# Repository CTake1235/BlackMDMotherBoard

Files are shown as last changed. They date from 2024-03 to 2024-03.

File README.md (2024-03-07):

# 黒MDマザーボード設計構想
> by しーたけ @C_Take_e
> since 2024/03/05
## 黒MDとは？
```
茨城高専ロボット部にて2017年に開発・製造されたMD。レジストが黒いのでそう呼ばれている。
定格12V駆動。I2C信号またはRS-485で動作する（基本I2Cでしか使わん）。
ロボコンで用いる各種モータを振り回せるため、何も考えずに使いまわされ続けている。
```
## コンセプト
- **やさしいマザボ**
## 詳細な構想
- ケーブルを介した連結が可能な、4枚挿しコンパクトマザボ
	- 単純なケーブルでできる、「マザー連結用」のようなケーブルを不要とする
	
- 黒MD初期マザーに準拠したコネクタ配線
- XAコネクタとXT60コネクタ（現在部活で主流のもの）を用いる
- 電源系の配線はタテ、信号系はヨコ
	- 電源系をヨコにすると、水平方向に広げる回路ボックスと相性が悪い
		- 縦に広がる回路ボックス: 基板を縦に積みつつコネクタを横に出して省面積化できる
		- 横に広がる回路ボックス(現在): 基板を水平方向に並べるので、コネクタがヨコ向きだとほかの基板と干渉するなど問題が起きやすい
	- 信号系はタテにすると基板の配置上MDとツメロック部分が干渉するなど、かえって邪魔になる
		- また、信号線は電源線に比べて細く曲げやすいため、ケーブルが他の基板などと干渉しにくい
- 100mm \* 100mmに収める
	- これは発注金額の問題
	- 実際には1.27(0.5mil)の倍数: 99.06mmを1辺とする設計にすることで配線の対称性などを保つ
- https://www.figma.com/file/h6nRyaCE1Uanp6SJ3a7Op9/2024%E9%BB%92MD%E3%83%9E%E3%82%B6%E3%83%BC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
	- figmaに謎図あります

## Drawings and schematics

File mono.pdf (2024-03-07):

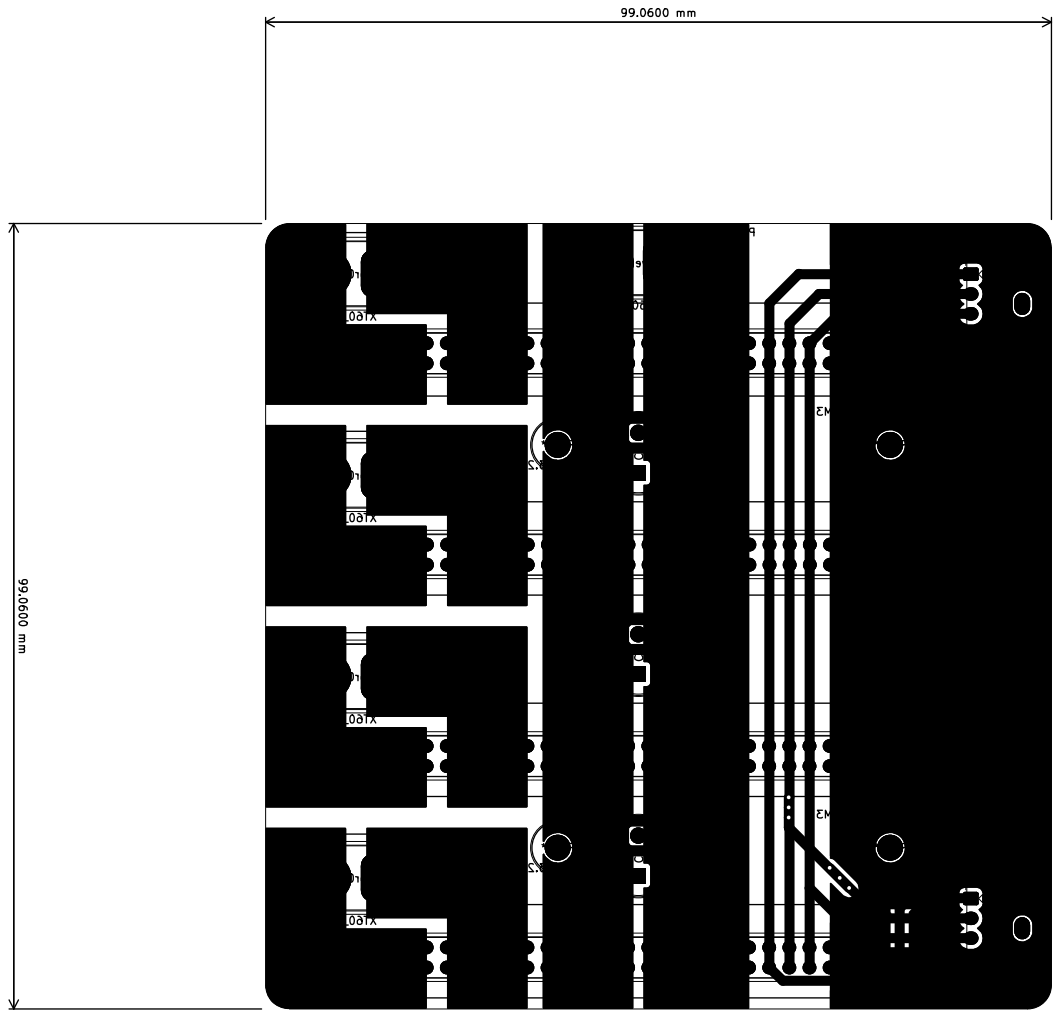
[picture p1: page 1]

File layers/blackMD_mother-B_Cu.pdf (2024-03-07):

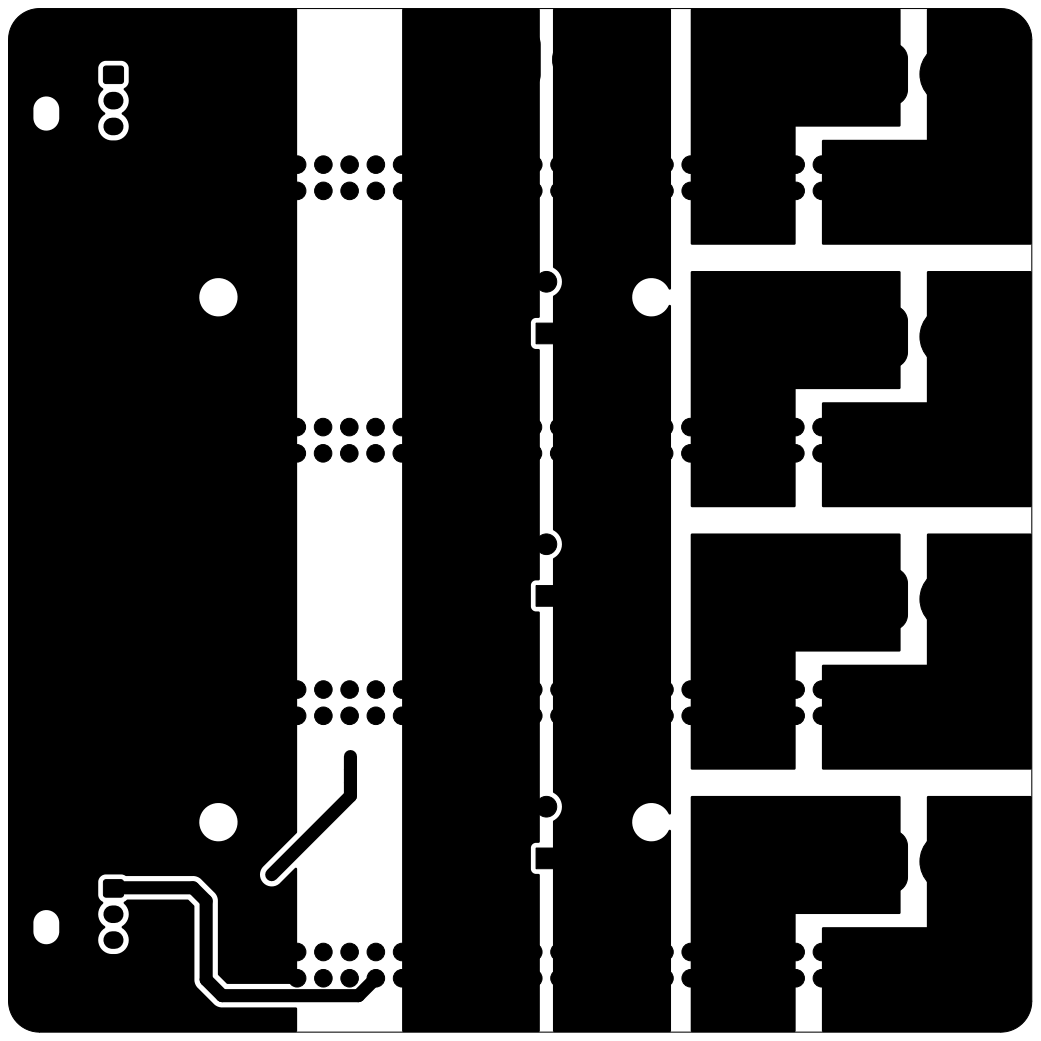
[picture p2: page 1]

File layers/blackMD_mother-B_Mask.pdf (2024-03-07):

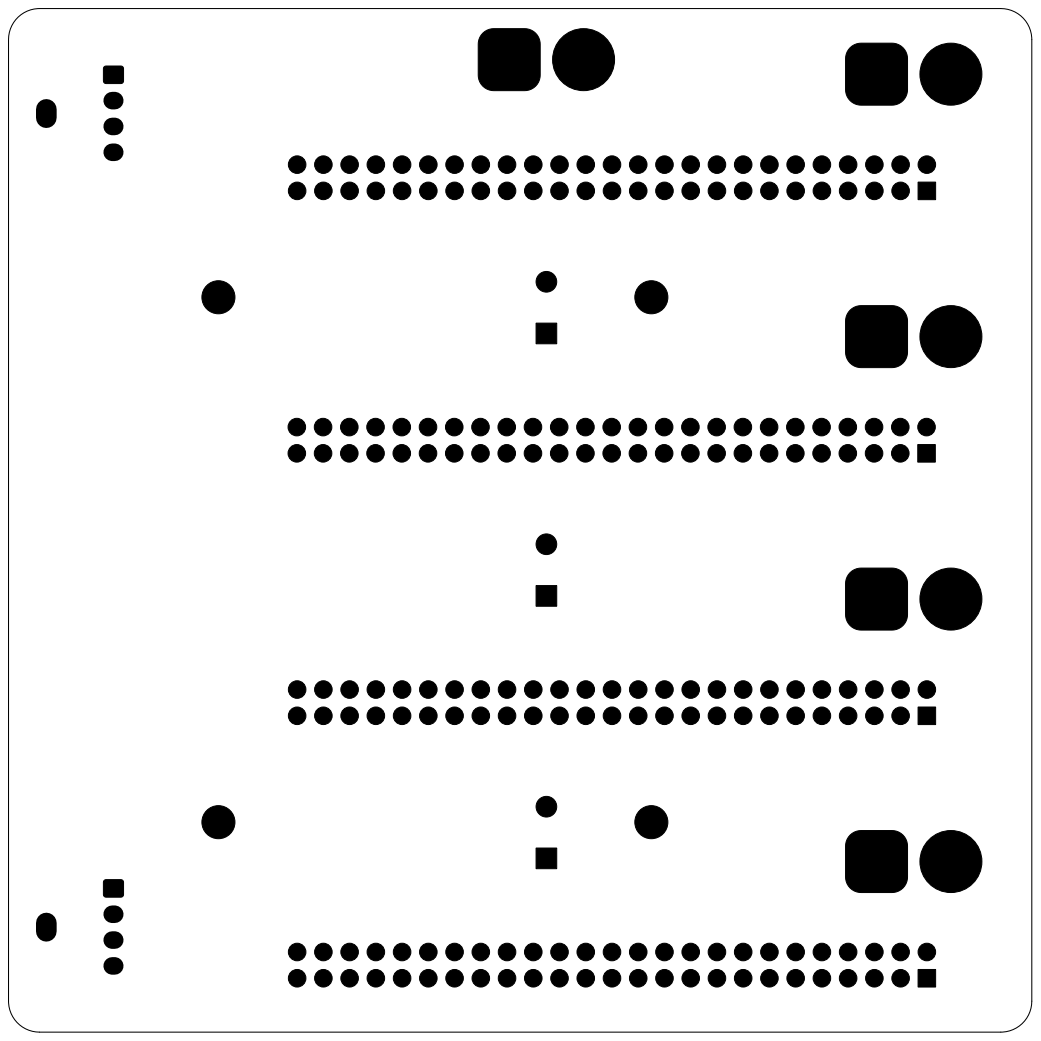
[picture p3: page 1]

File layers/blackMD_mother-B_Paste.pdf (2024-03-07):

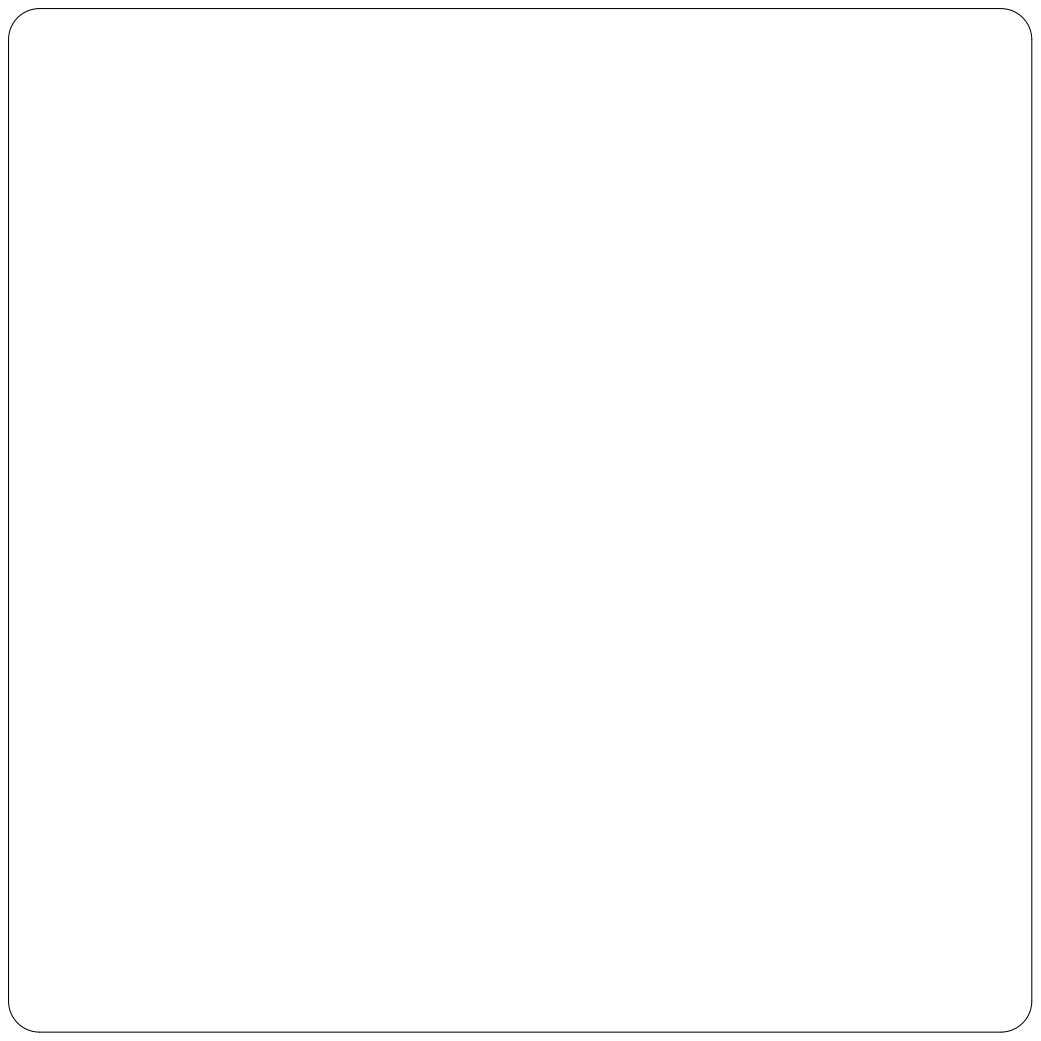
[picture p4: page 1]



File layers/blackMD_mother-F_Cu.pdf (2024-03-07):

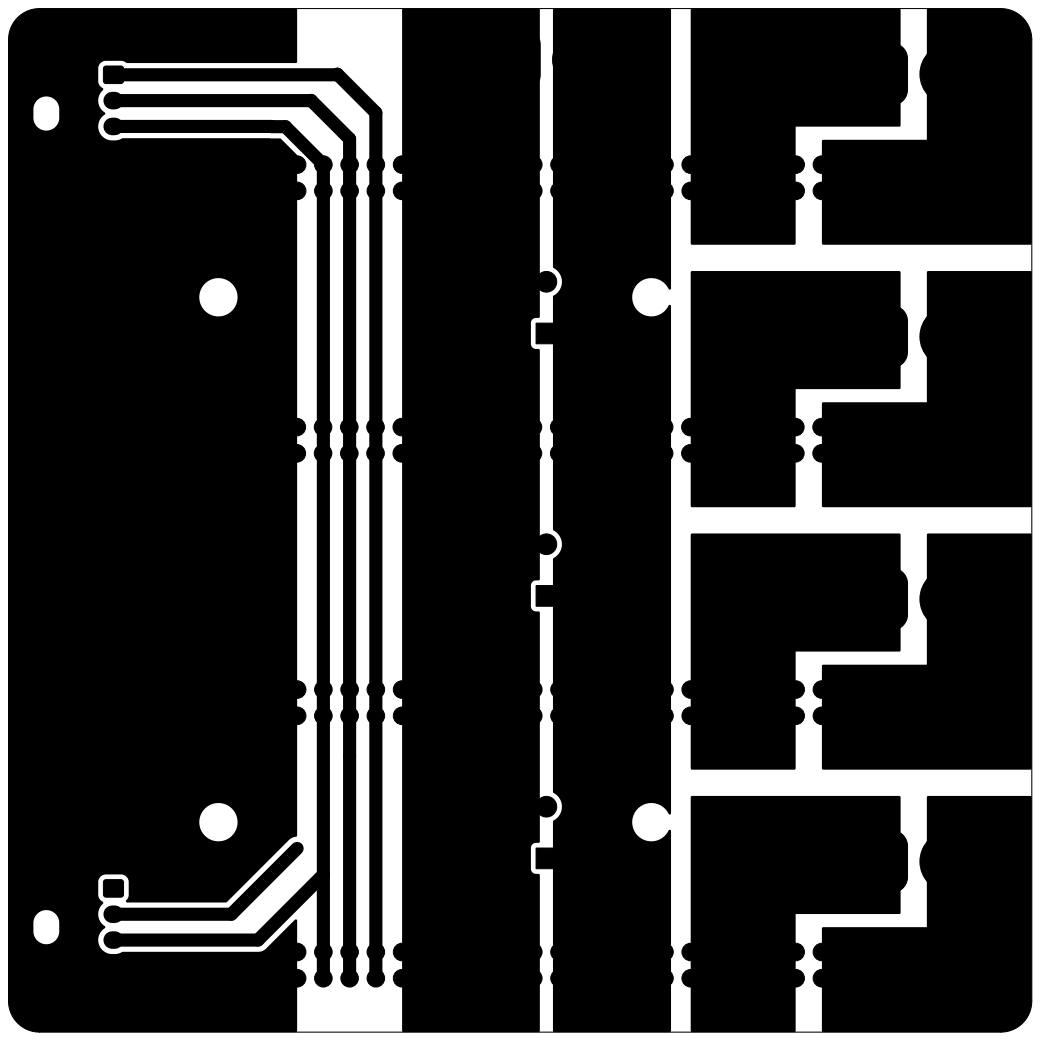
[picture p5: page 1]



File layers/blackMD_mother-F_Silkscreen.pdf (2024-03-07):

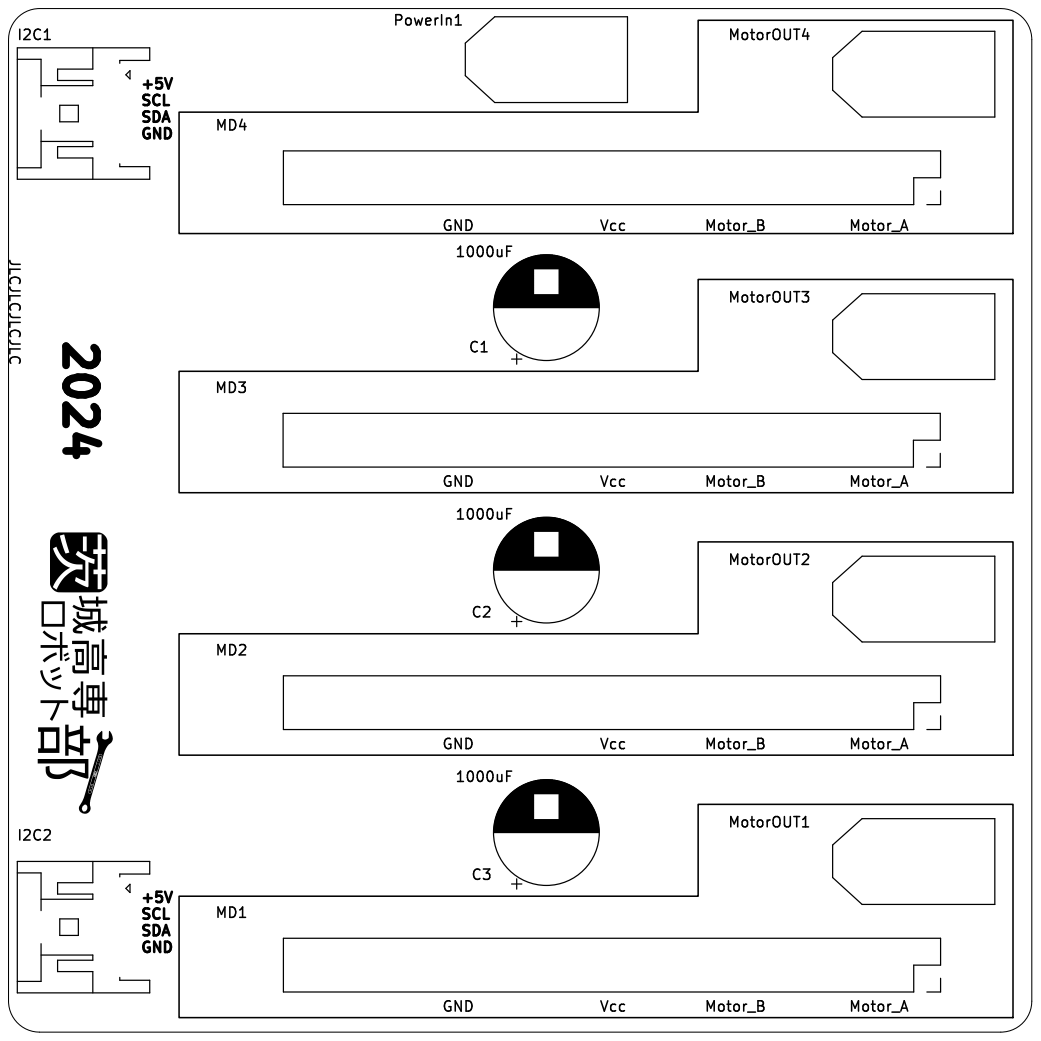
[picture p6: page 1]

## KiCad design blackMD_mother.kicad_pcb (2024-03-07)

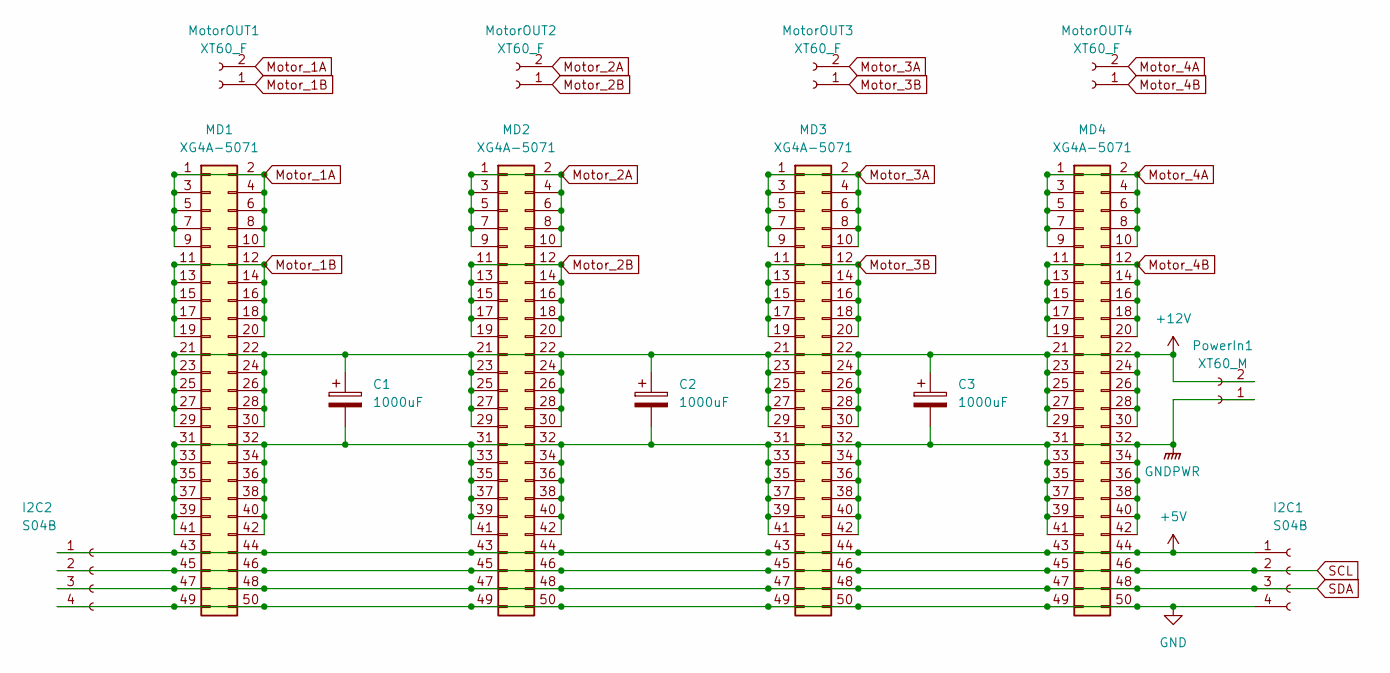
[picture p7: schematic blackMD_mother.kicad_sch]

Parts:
C1, C2, C3: 1000uF; CP_Radial_D10.0mm_P5.00mm
I2C1, I2C2: S04B; JST_XA_S04B-XASK-1_1x04_P2.50mm_Horizontal
MD1, MD2, MD3, MD4: XG4A-5071; PinSocket_2x25_P2.54mm_Vertical
MotorOUT1, MotorOUT2, MotorOUT3, MotorOUT4: XT60_F; AMASS_XT60-F_1x02_P7.20mm_Vertical
PowerIn1: XT60_M; AMASS_XT60-M_1x02_P7.20mm_Vertical

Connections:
+5V: I2C1.1, I2C2.1, MD1.43, MD1.44, MD2.43, MD2.44, MD3.43, MD3.44, MD4.43, MD4.44
+12V: C1.1, C2.1, C3.1, MD1.21, MD1.22, MD1.23, MD1.24, MD1.25, MD1.26, MD1.27, MD1.28, MD1.29, MD1.30, MD2.21, MD2.22, MD2.23, MD2.24, MD2.25, MD2.26, MD2.27, MD2.28, MD2.29, MD2.30, MD3.21, MD3.22, MD3.23, MD3.24, MD3.25, MD3.26, MD3.27, MD3.28, MD3.29, MD3.30, MD4.21, MD4.22, MD4.23, MD4.24, MD4.25, MD4.26, MD4.27, MD4.28, MD4.29, MD4.30, PowerIn1.2
GND: I2C1.4, I2C2.4, MD1.49, MD1.50, MD2.49, MD2.50, MD3.49, MD3.50, MD4.49, MD4.50
GNDPWR: C1.2, C2.2, C3.2, MD1.31, MD1.32, MD1.33, MD1.34, MD1.35, MD1.36, MD1.37, MD1.38, MD1.39, MD1.40, MD1.41, MD1.42, MD2.31, MD2.32, MD2.33, MD2.34, MD2.35, MD2.36, MD2.37, MD2.38, MD2.39, MD2.40, MD2.41, MD2.42, MD3.31, MD3.32, MD3.33, MD3.34, MD3.35, MD3.36, MD3.37, MD3.38, MD3.39, MD3.40, MD3.41, MD3.42, MD4.31, MD4.32, MD4.33, MD4.34, MD4.35, MD4.36, MD4.37, MD4.38, MD4.39, MD4.40, MD4.41, MD4.42, PowerIn1.1
Motor_1A: MD1.1, MD1.2, MD1.3, MD1.4, MD1.5, MD1.6, MD1.7, MD1.8, MD1.9, MD1.10, MotorOUT1.2
Motor_1B: MD1.11, MD1.12, MD1.13, MD1.14, MD1.15, MD1.16, MD1.17, MD1.18, MD1.19, MD1.20, MotorOUT1.1
Motor_2A: MD2.1, MD2.2, MD2.3, MD2.4, MD2.5, MD2.6, MD2.7, MD2.8, MD2.9, MD2.10, MotorOUT2.2
Motor_2B: MD2.11, MD2.12, MD2.13, MD2.14, MD2.15, MD2.16, MD2.17, MD2.18, MD2.19, MD2.20, MotorOUT2.1
Motor_3A: MD3.1, MD3.2, MD3.3, MD3.4, MD3.5, MD3.6, MD3.7, MD3.8, MD3.9, MD3.10, MotorOUT3.2
Motor_3B: MD3.11, MD3.12, MD3.13, MD3.14, MD3.15, MD3.16, MD3.17, MD3.18, MD3.19, MD3.20, MotorOUT3.1
Motor_4A: MD4.1, MD4.2, MD4.3, MD4.4, MD4.5, MD4.6, MD4.7, MD4.8, MD4.9, MD4.10, MotorOUT4.2
Motor_4B: MD4.11, MD4.12, MD4.13, MD4.14, MD4.15, MD4.16, MD4.17, MD4.18, MD4.19, MD4.20, MotorOUT4.1
SCL: I2C1.2, I2C2.2, MD1.45, MD1.46, MD2.45, MD2.46, MD3.45, MD3.46, MD4.45, MD4.46
SDA: I2C1.3, I2C2.3, MD1.47, MD1.48, MD2.47, MD2.48, MD3.47, MD3.48, MD4.47, MD4.48

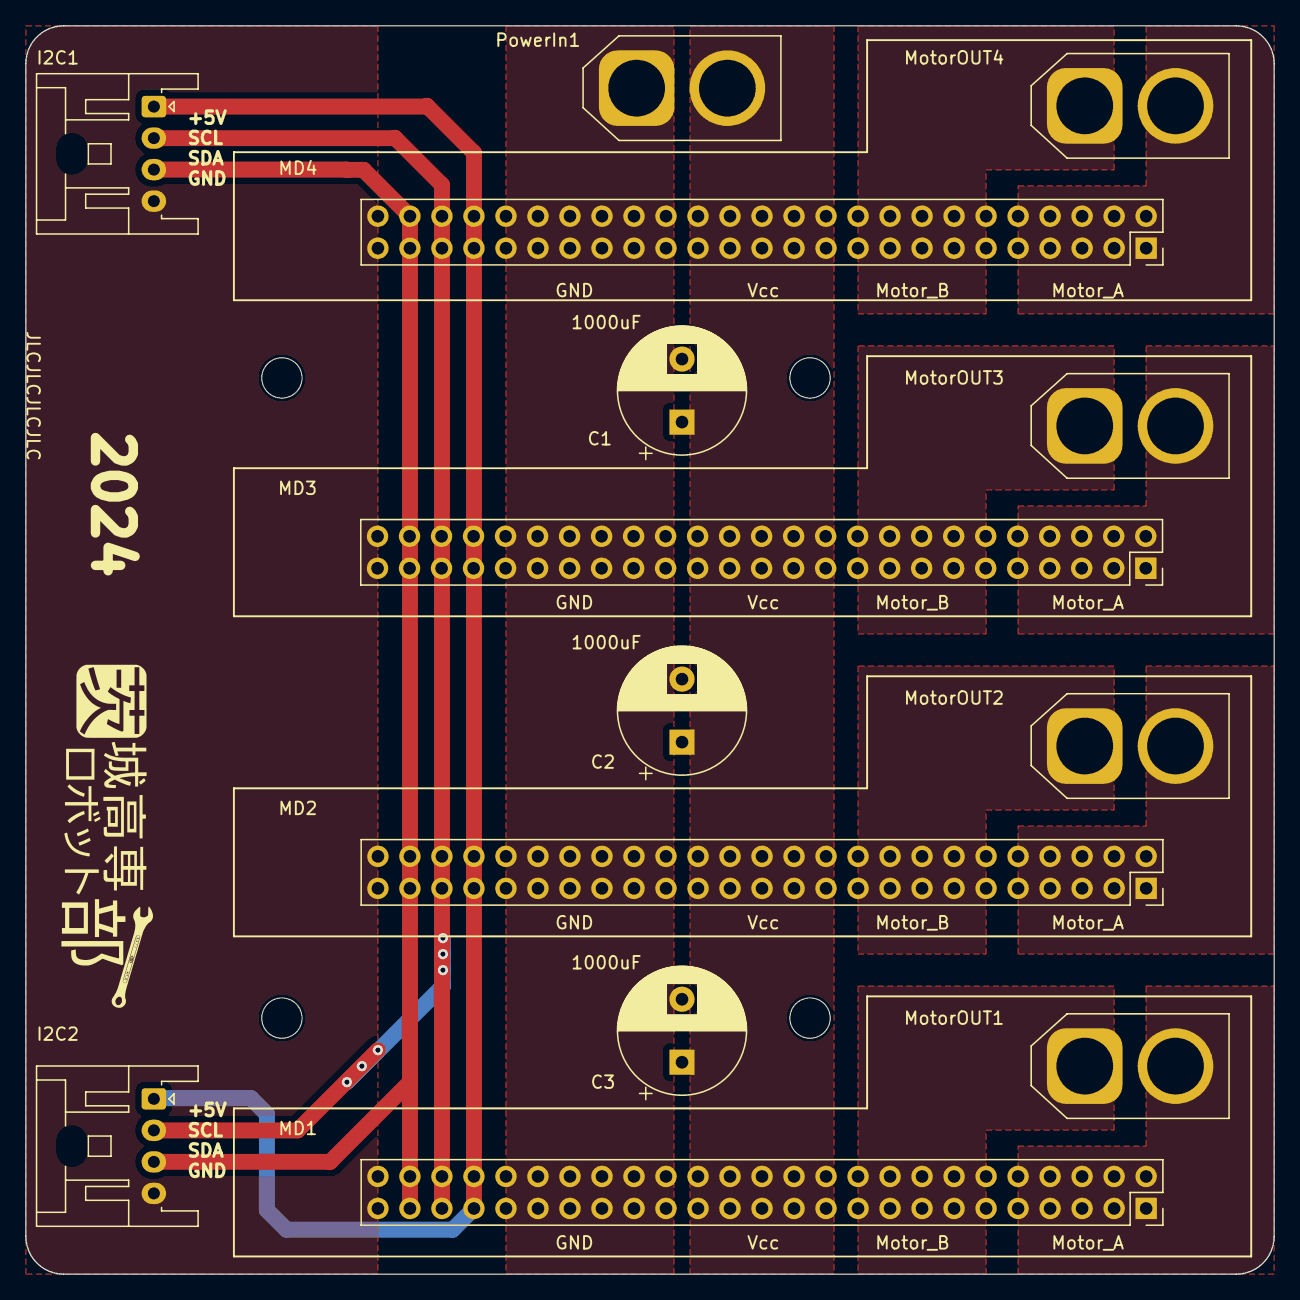
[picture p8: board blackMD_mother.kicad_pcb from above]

Board: 2 copper layers, 99.1 x 99.1 mm, 14 parts (0 on the bottom side), 14 nets.

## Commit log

2024-03-06 update: PDFs, GBRs
    [blackMD_mother-B_Cu.gbr, blackMD_mother-B_Mask.gbr, blackMD_mother-B_Paste.gbr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]
2024-03-06 change: fillet corners
    [blackMD_mother.kicad_pcb]
2024-03-06 update: PDFs & GBRs
    [blackMD_mother-B_Cu.gbr, blackMD_mother-B_Mask.gbr, blackMD_mother-B_Paste.gbr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]
2024-03-06 change: width of GNDPWR
    [blackMD_mother-B_Cu.gbr, blackMD_mother-B_Mask.gbr, blackMD_mother-B_Paste.gbr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]
2024-03-07 Revert "change: width of GNDPWR"
    This reverts commit 1e5340b1a1ce9a68678be1db281a547735c12933.
    [blackMD_mother-B_Cu.gbr, blackMD_mother-B_Mask.gbr, blackMD_mother-B_Paste.gbr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]
2024-03-07 swap MotorA & MotorB
    [blackMD_mother.kicad_pcb, blackMD_mother.kicad_sch]
2024-03-07 update PDFs & GBRs
    [blackMD_mother-B_Cu.gbr, blackMD_mother-B_Mask.gbr, blackMD_mother-B_Paste.gbr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]
2024-03-07 add JLC
    [blackMD_mother-B_Cu.gbr, blackMD_mother-B_Mask.gbr, blackMD_mother-B_Paste.gbr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]
2024-03-07 update silk
    [blackMD_mother.kicad_pcb, blackMD_mother.kicad_sch]
2024-03-07 keep more clearance between +5V & GNDPWR
    [blackMD_mother-B_Cu.gbr, blackMD_mother-B_Mask.gbr, blackMD_mother-B_Paste.gbr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]
